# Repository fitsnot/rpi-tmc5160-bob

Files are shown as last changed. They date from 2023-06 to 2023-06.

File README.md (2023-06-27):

# rpi-tmc5160-bob
Quick and dirty stepper motor controller based on Raspberry Pi Pico and Trinamic TMC5160-BOB [PCB] [ARDUINO]
The goal is to have either a potentiometer or magentic encoder as rotary input that controls the speed of a large stepper motor. SPI and the integrated motion controller of the Trinamic TMC5160 is used to reduce computational load on the MCU as low as possible.

## Code
The TMC5160_Arduino library by tommag https://github.com/tommag/TMC5160_Arduino is used.

TODO:
- [x] Initial test with RPI and TMC5160-BOB
- [ ] Integrate AS5600 as rotary encoder
- [ ] Tune for utilised MOSFETS

## PCB
FIrst draft uses Raspberry Pi Pico and either a TMC5160-BOB ("Breakout board") or a corresponding SilentStepstick. A AS5600 can be used as a rotary encoder via I2C protocol.

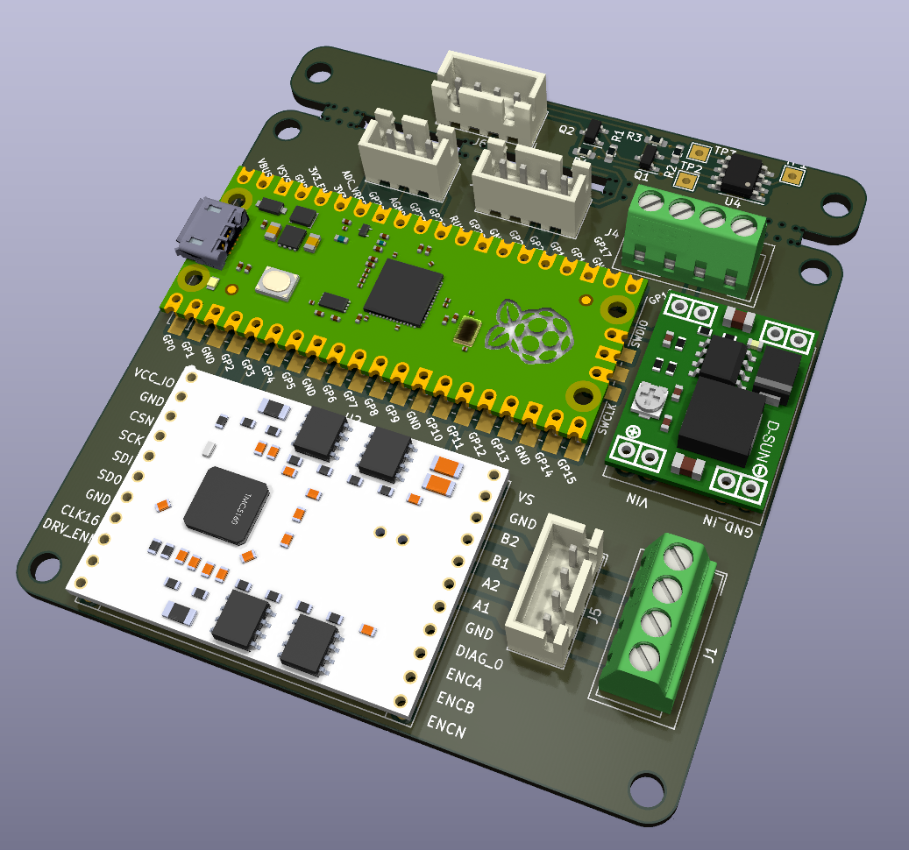
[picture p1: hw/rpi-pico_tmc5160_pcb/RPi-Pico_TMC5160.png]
Rendering of the PCB


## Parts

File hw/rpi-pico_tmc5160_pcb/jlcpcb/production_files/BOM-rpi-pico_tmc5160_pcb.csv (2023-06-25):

Comment | Designator | Footprint | LCSC
Conn_01x03 | J2 | JST_XH_B3B-XH-A_1x03_P2.50mm_Vertical | C144394
Conn_01x04 | J3,J5,J6 | JST_XH_B4B-XH-A_1x04_P2.50mm_Vertical | C144395
4k7 | R1,R2,R3,R4 | R_0603_1608Metric_Pad0.98x0.95mm_HandSolder | C23162
AS5600 | U4 | SOIC-8_3.9x4.9mm_P1.27mm | C499458
Conn_01x04 | J1,J4 | Wago_734-134_1x04_P3.50mm_Vertical | C557656
2N7002 | Q1,Q2 | SOT-23 | C8545
MountingHole | H6 | MountingHole_3.2mm_M3_ISO7380
MountingHole | H5 | MountingHole_3.2mm_M3_ISO7380
MountingHole | H4 | MountingHole_3.2mm_M3_ISO7380
MountingHole | H3 | MountingHole_3.2mm_M3_ISO7380
MountingHole | H2 | MountingHole_3.2mm_M3_ISO7380
MountingHole | H1 | MountingHole_3.2mm_M3_ISO7380
TestPoint | TP3 | TestPoint_THTPad_2.0x2.0mm_Drill1.0mm
MP1584 | U3 | MP1584_MOD
Housing | N1 | Mousebite
Housing | N4 | Mousebite
TestPoint | TP1 | TestPoint_THTPad_2.0x2.0mm_Drill1.0mm
~ | U2 | TMC5160-BOB
Housing | N2 | Mousebite
Pico | U1 | RPi_Pico_SMD_TH
Housing | N3 | Mousebite
TestPoint | TP2 | TestPoint_THTPad_2.0x2.0mm_Drill1.0mm

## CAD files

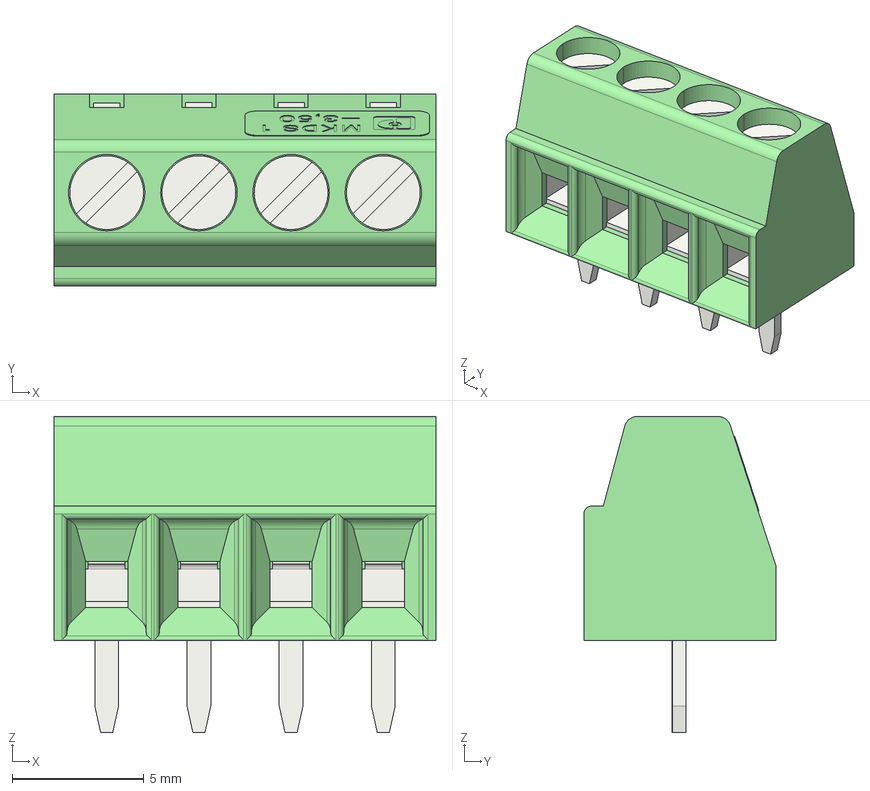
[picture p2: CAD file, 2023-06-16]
hw/rpi-pico_tmc5160_pcb/3dmodels/pxc_1751264_04_MKDS-1-4-3-5_3D.stp
14.5 x 7.30 x 12.0 mm

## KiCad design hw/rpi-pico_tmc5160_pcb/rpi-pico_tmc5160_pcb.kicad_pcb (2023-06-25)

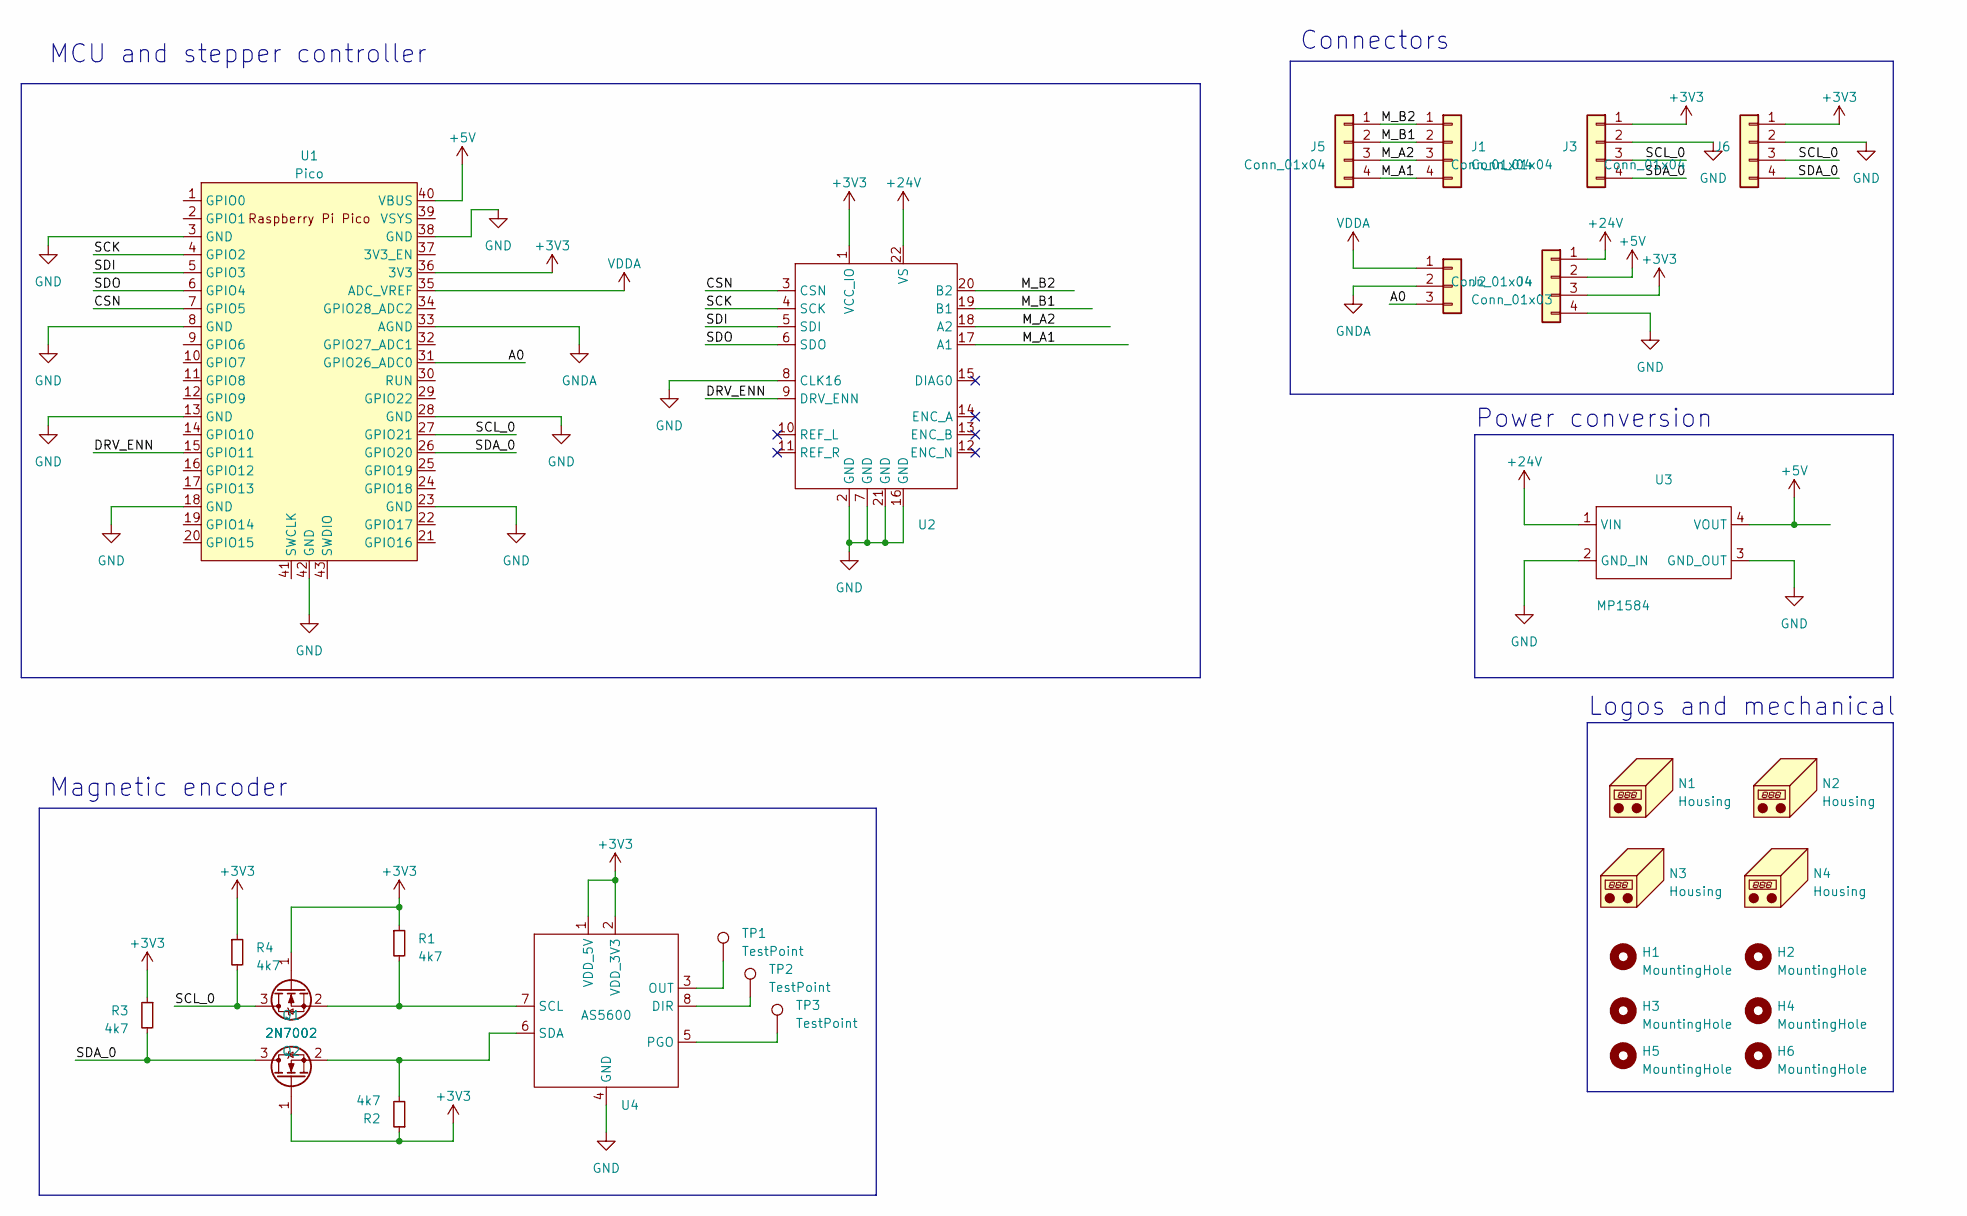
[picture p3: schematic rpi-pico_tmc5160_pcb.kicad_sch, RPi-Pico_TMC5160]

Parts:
H1, H2, H3, H4, H5, H6: MountingHole; MountingHole_3.2mm_M3_ISO7380
J1, J4: Conn_01x04; Wago_734-134_1x04_P3.50mm_Vertical; LCSC C557656
J2: Conn_01x03; JST_XH_B3B-XH-A_1x03_P2.50mm_Vertical; LCSC C144394
J3, J5, J6: Conn_01x04; JST_XH_B4B-XH-A_1x04_P2.50mm_Vertical; LCSC C144395
N1, N2, N3, N4: Housing; Mousebite
Q1, Q2: 2N7002; SOT-23; LCSC C8545
R1, R2, R3, R4: 4k7; R_0603_1608Metric_Pad0.98x0.95mm_HandSolder
TP1, TP2, TP3: TestPoint; TestPoint_THTPad_2.0x2.0mm_Drill1.0mm
U1: Pico; RPi_Pico_SMD_TH
U2: TMC5160-BOB
U3: MP1584; MP1584_MOD
U4: AS5600; SOIC-8_3.9x4.9mm_P1.27mm

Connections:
+3V3: J3.1, J4.3, J6.1, Q1.1 (G), Q2.1 (G), R1.1, R2.1, R3.1, R4.1, U1.36 (3V3), U2.1 (VCC_IO), U4.1 (VDD_5V), U4.2 (VDD_3V3)
+5V: J4.2, U1.40 (VBUS), U3.4 (VOUT)
+24V: J4.1, U2.22 (VS), U3.1 (VIN)
/A0: J2.3, U1.31 (GPIO26_ADC0)
/CSN: U1.7 (GPIO5), U2.3 (CSN)
/DRV_ENN: U1.15 (GPIO11), U2.9 (DRV_ENN)
/M_A1: J1.4, J5.4, U2.17 (A1)
/M_A2: J1.3, J5.3, U2.18 (A2)
/M_B1: J1.2, J5.2, U2.19 (B1)
/M_B2: J1.1, J5.1, U2.20 (B2)
/SCK: U1.4 (GPIO2), U2.4 (SCK)
/SCL_0: J3.3, J6.3, Q2.3 (D), R4.2, U1.27 (GPIO21)
/SDA_0: J3.4, J6.4, Q1.3 (D), R3.2, U1.26 (GPIO20)
/SDI: U1.5 (GPIO3), U2.5 (SDI)
/SDO: U1.6 (GPIO4), U2.6 (SDO)
GND: J3.2, J4.4, J6.2, U1.3 (GND), U1.8 (GND), U1.13 (GND), U1.18 (GND), U1.23 (GND), U1.28 (GND), U1.38 (GND), U1.42 (GND), U2.2 (GND), U2.7 (GND), U2.8 (CLK16), U2.16 (GND), U2.21 (GND), U3.2 (GND_IN), U3.3 (GND_OUT), U4.4 (GND)
GNDA: J2.2, U1.33 (AGND)
unnamed: Q1.2 (S), R2.2, U4.6 (SDA)
unnamed: Q2.2 (S), R1.2, U4.7 (SCL)
unnamed: TP2.1, U4.8 (DIR)
unnamed: TP1.1, U4.3 (OUT)
unnamed: TP3.1, U4.5 (PGO)
VDDA: J2.1, U1.35 (ADC_VREF)

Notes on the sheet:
MCU and stepper controller
Connectors
Power conversion
Logos and mechanical
Magnetic encoder

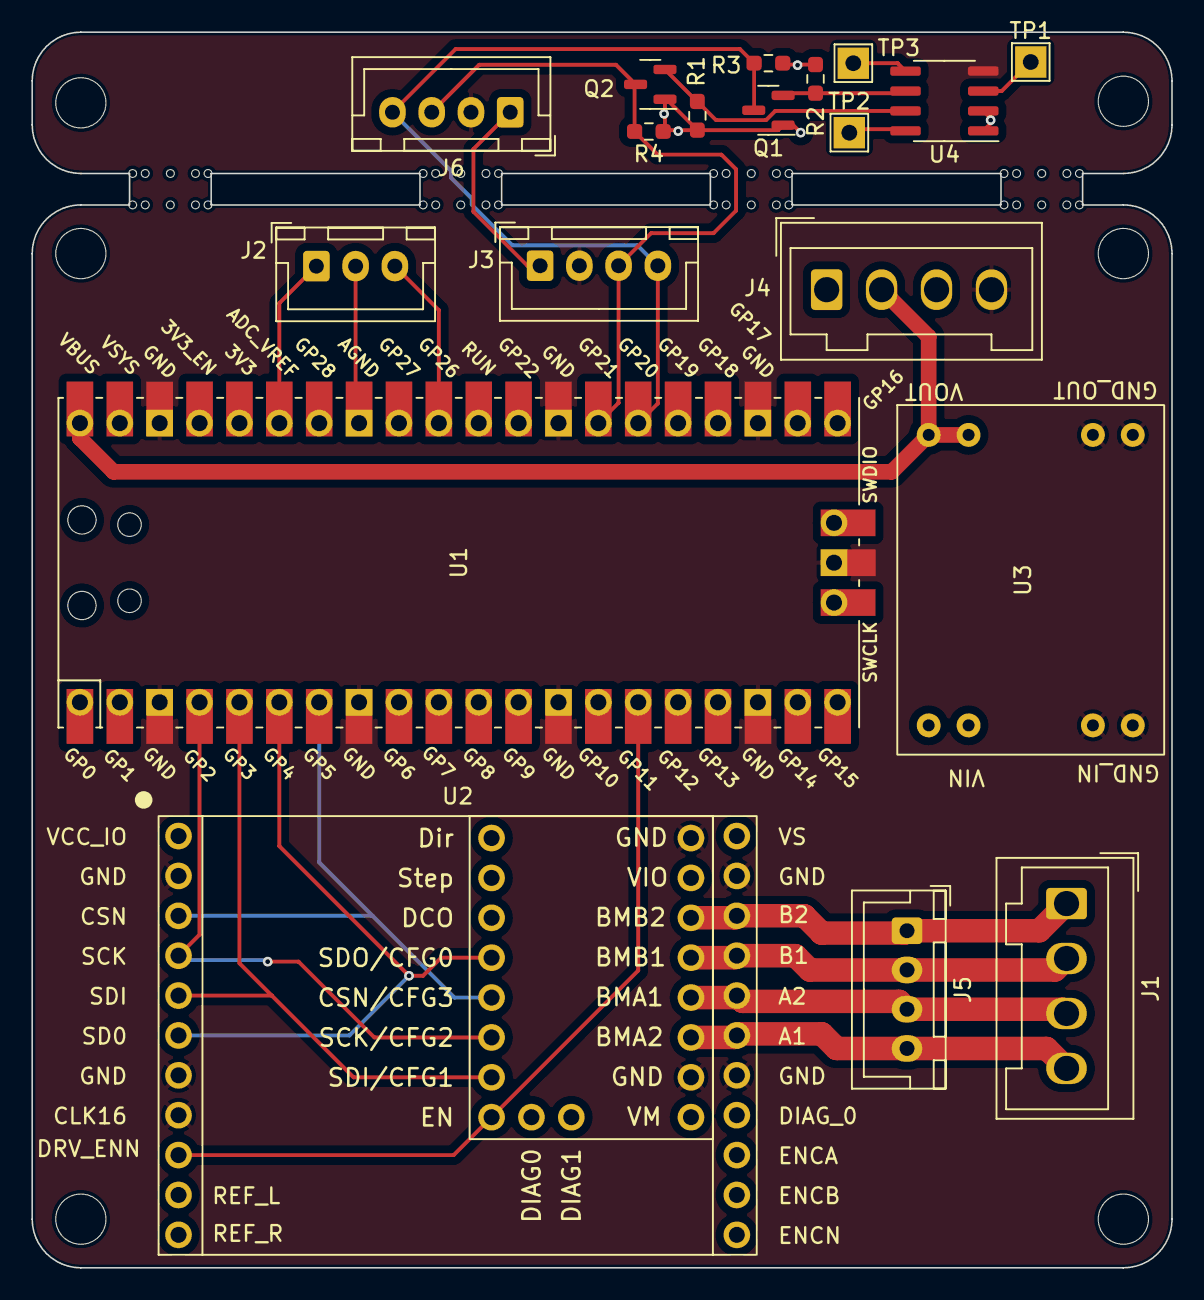
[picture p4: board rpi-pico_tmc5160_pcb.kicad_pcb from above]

Board: 4 copper layers, 72.6 x 78.7 mm, 29 parts (0 on the bottom side), 23 nets.

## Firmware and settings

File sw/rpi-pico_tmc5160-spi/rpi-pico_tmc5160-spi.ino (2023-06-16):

/* TMC5160 SPI example

This code demonstrates the usage of a Trinamic TMC5160 stepper driver in SPI mode.

Hardware setup :
Connect the following lines between the microcontroller board and the TMC5160 driver
(Tested with a Teensy 3.2 and a TMC5160-BOB)

  MOSI (Teensy : 11)  <=> SDI
  MISO (Teensy : 12)  <=> SDO
  SCK (Teensy : 13)   <=> SCK
  5                   <=> CSN
  8                   <=> DRV_ENN (optional, tie to GND if not used)
  GND                 <=> GND
  3.3V/5V             <=> VCC_IO (depending on the processor voltage)

The TMC5160 VS pin must also be powered.
Tie CLK16 to GND to use the TMC5160 internal clock.
Tie SPI_MODE to VCC_IO, SD_MODE to GND.

Please run the Config Wizard for power stage fine tuning / motor calibration (this code uses the default parameters and auto calibration).

Copyright (c) 2020 Tom Magnier

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
THE SOFTWARE IS PROVIDED "AS IS", WITHOUT WARRANTY OF ANY KIND, EXPRESS OR
IMPLIED, INCLUDING BUT NOT LIMITED TO THE WARRANTIES OF MERCHANTABILITY,
FITNESS FOR A PARTICULAR PURPOSE AND NONINFRINGEMENT. IN NO EVENT SHALL THE
AUTHORS OR COPYRIGHT HOLDERS BE LIABLE FOR ANY CLAIM, DAMAGES OR OTHER
LIABILITY, WHETHER IN AN ACTION OF CONTRACT, TORT OR OTHERWISE, ARISING FROM,
OUT OF OR IN CONNECTION WITH THE SOFTWARE OR THE USE OR OTHER DEALINGS IN THE
SOFTWARE.
*/

#include <Arduino.h>
#include <TMC5160.h>
#include <PicoSPI.h>

const uint8_t SPI_CS = 5;        // CS pin in SPI mode
const uint8_t SPI_DRV_ENN = 11;  // DRV_ENN pin in SPI mode
const uint8_t spi_MOSI = 3;
const uint8_t spi_MISO = 4;
const uint8_t spi_SCK = 2;

TMC5160_SPI motor = TMC5160_SPI(SPI_CS);  //Use default SPI peripheral and SPI settings.

char buf[80];

int readline(int readch, char *buffer, int len) {
  static int pos = 0;
  int rpos;

  if (readch > 0) {
    switch (readch) {
      case '\r':  // Ignore CR
        break;
      case '\n':  // Return on new-line
        rpos = pos;
        pos = 0;  // Reset position index ready for next time
        return rpos;
      default:
        if (pos < len - 1) {
          buffer[pos++] = readch;
          buffer[pos] = 0;
        }
    }
  }
  return 0;
}

void setup() {
  // USB/debug serial coms
  Serial.begin(115200);

  pinMode(SPI_DRV_ENN, OUTPUT);
  digitalWrite(SPI_DRV_ENN, LOW);  // Active low

  // This sets the motor & driver parameters /!\ run the configWizard for your driver and motor for fine tuning !
  TMC5160::PowerStageParameters powerStageParams;  // defaults.
  TMC5160::MotorParameters motorParams;
  powerStageParams.drvStrength = 0;
  powerStageParams.bbmTime = 0;
  powerStageParams.bbmClks = 0;
  motorParams.globalScaler = 255;
  motorParams.irun = 15;
  motorParams.ihold = 0;
  motorParams.freewheeling = TMC5160_Reg::FREEWHEEL_ENABLED;
  motorParams.pwmOfsInitial = 74;
  motorParams.pwmGradInitial = 75;
  motor.begin(powerStageParams, motorParams, TMC5160::NORMAL_MOTOR_DIRECTION);
  //motorParams.globalScaler = 255;  // Adapt to your driver and motor (check TMC5160 datasheet - "Selecting sense resistors")
  //motorParams.irun = 31;
  motorParams.ihold = 15;
  SPI.setRX(spi_MISO);
  SPI.setTX(spi_MOSI);
  SPI.setSCK(spi_SCK);
  SPI.setCS(SPI_CS);
  //  PicoSPI0.configure(spi_SCK, spi_MOSI, spi_MISO, SPI_CS, 1000000, 0, false);

  SPI.begin();
  motor.begin(powerStageParams, motorParams, TMC5160::NORMAL_MOTOR_DIRECTION);

  // ramp definition
  motor.setRampMode(TMC5160::VELOCITY_MODE);
  motor.setMaxSpeed(0);
  motor.setAcceleration(3000);

  delay(1000);  // Standstill for automatic tuning
}

void loop() {
  uint32_t now = millis();
  static unsigned long t_dirchange, t_echo;
  static bool dir;

  // every n seconds or so...
  if (now - t_dirchange > 3000) {
    t_dirchange = now;

    // reverse direction
    dir = !dir;
    motor.setTargetPosition(dir ? 2000 : 0);  // 1 full rotation = 200s/rev
  }
  
  int val = analogRead(26);
  Serial.println(val);
  float val_map = map(val, 3, 1023, 0, 614); 
  float vactual = motor.getCurrentSpeed();
  if (val_map == 0) {
    motor.setMaxSpeed(val_map);

 
  }
  if (val_map != vactual) {
    motor.setMaxSpeed(val_map);

  }

  if (readline(Serial.read(), buf, 80) > 0) {

    Serial.print(buf);
    float speed;
    speed = (float)atof(buf);
    motor.setMaxSpeed(speed);
  }
}

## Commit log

2023-06-16 initial comit
    [pxc_1751264_04_MKDS-1-4-3-5_3D.stp, rpi-pico_tmc5160_pcb.kicad_pcb, rpi-pico_tmc5160_pcb.kicad_sch]
2023-06-25 first PCB layout
    [BOM-rpi-pico_tmc5160_pcb.csv, rpi-pico_tmc5160_pcb.kicad_pcb, rpi-pico_tmc5160_pcb.kicad_sch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]

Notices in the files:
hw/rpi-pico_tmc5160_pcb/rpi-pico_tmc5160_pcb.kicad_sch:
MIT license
